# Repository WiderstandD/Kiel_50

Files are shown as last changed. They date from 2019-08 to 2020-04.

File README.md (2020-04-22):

# Kiel_50 - Programmable ESC for the BLDC and PMSM Motors
Kiel 50 is an Arduino UNO shield for driving sensor-less three-phase BLDC motor. The main advantage is the sinusoidal current drive. By monitoring the back-EMF (BEMF) the motor can run without the independent rotor position sensor aka hall sensor or encoder. The chip is able to sense the BEMF from very low rpm up to high rpm. The speed can be set and adjusted using PWM or SPI. The Kiel 50 shield comes with the main chip [A4964](https://www.allegromicro.com/en/Products/Motor-Drivers/BLDC-Drivers/A4964) from "Allegro MicroSystems". This chip is All-in-one: the motor controller, N-Channel MOSFET driver, voltage regulator, MCU watchdog. The ability to program this chip via SPI using Arduino makes it easy to use for many projects. After the configurations were uploaded to the controller and saved to the NVM it can run without Arduino as well.

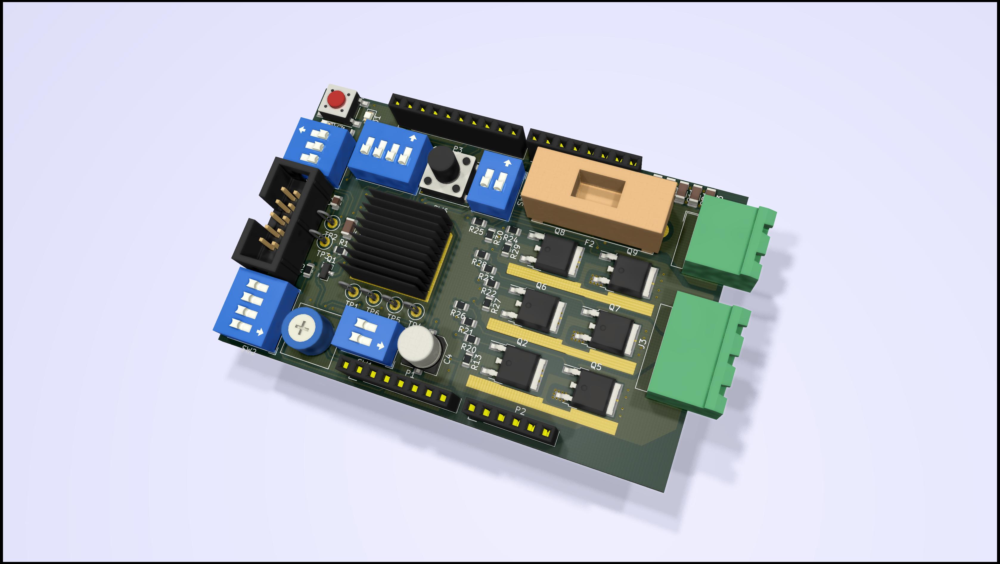
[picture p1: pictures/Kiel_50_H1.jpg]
Board_1

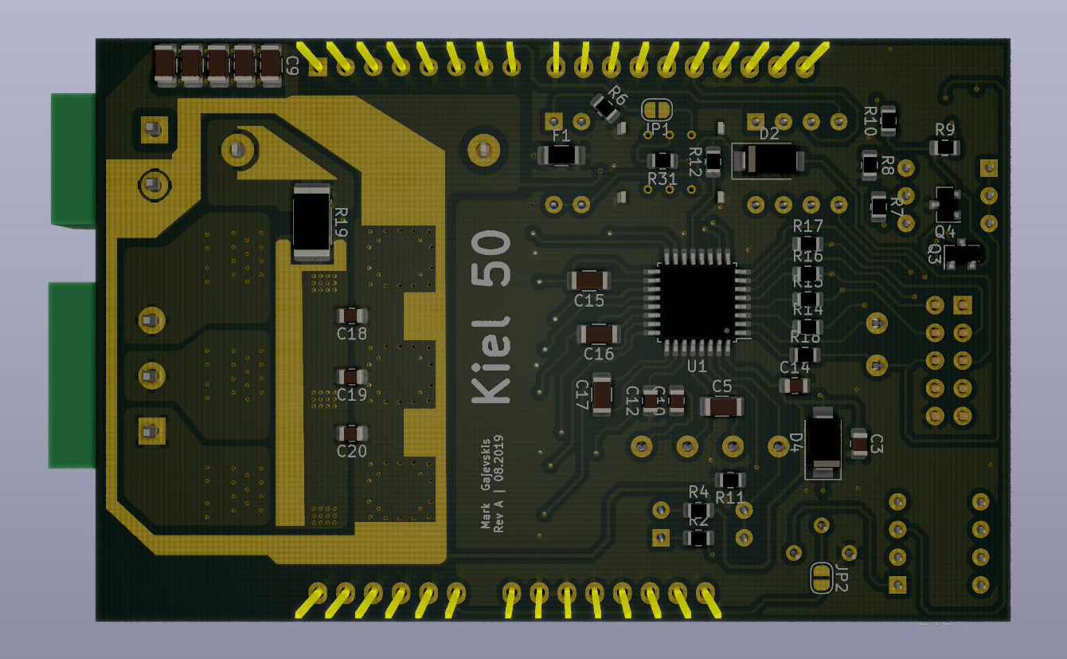
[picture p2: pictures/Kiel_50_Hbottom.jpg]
Board_2

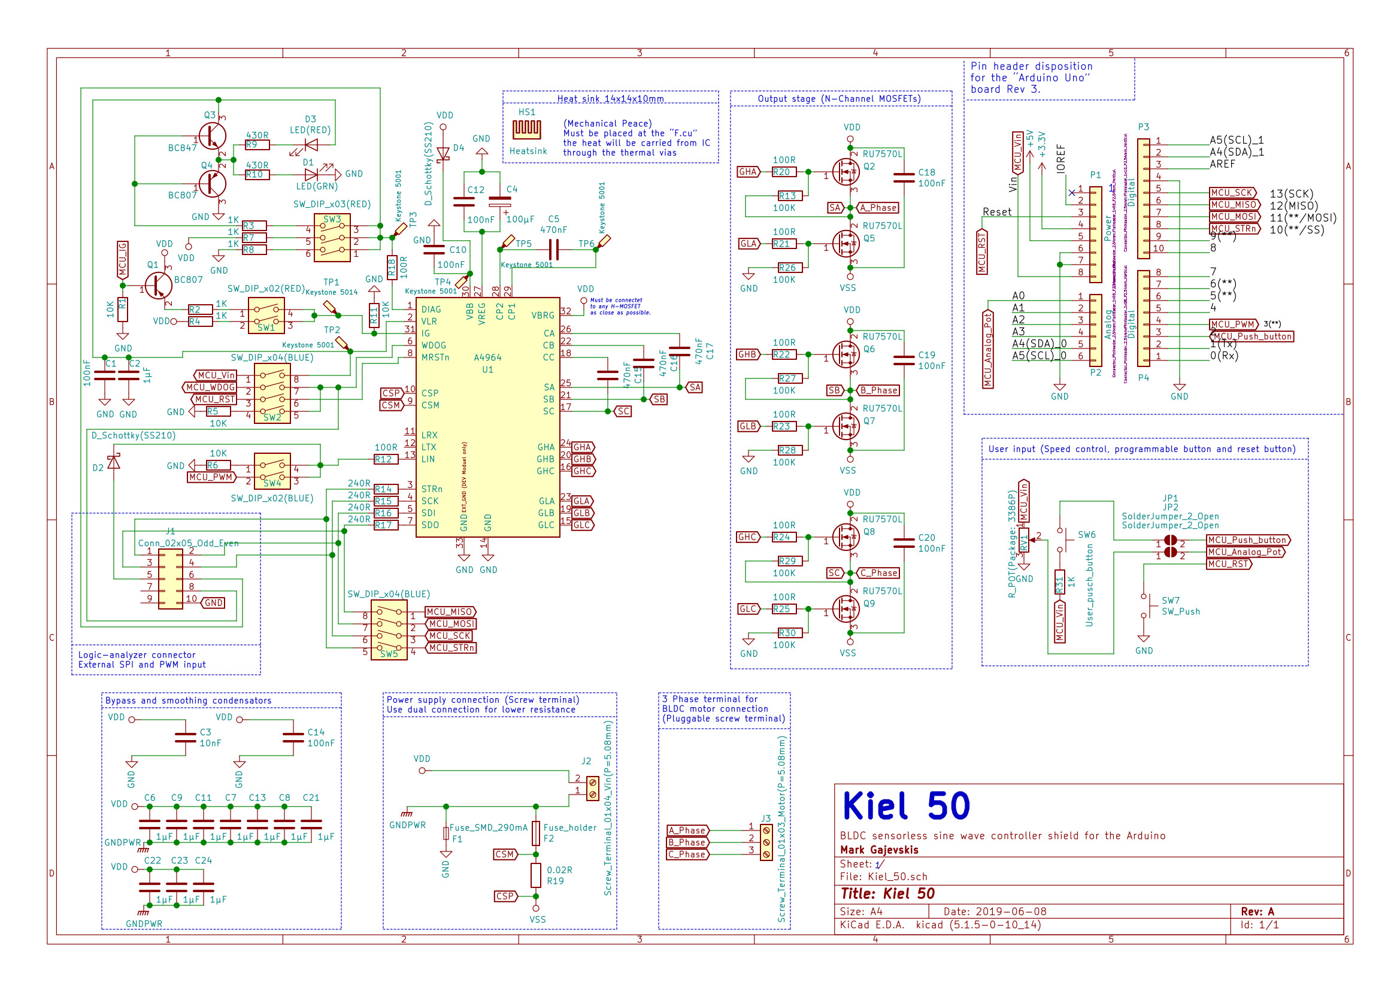
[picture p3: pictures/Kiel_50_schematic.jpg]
Board_3


Measurement of the three-phase (Voltage Ch.1,2,3)

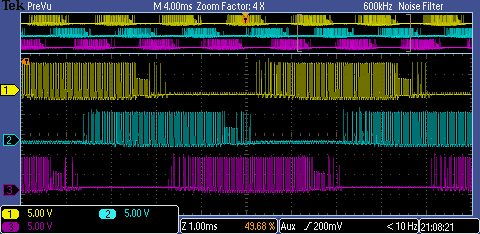
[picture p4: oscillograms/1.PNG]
Measurement1


Measurment of the three-phase (Voltage Ch.1,2,3 + Current Ch.4 (GN))
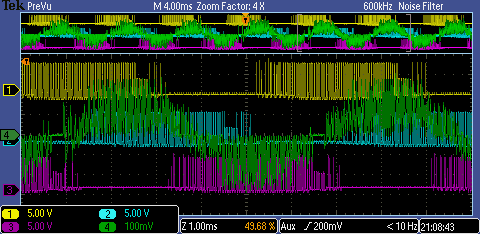
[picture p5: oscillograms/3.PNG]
Measurement2


---

# Technical specification
|Characteristic|Symbol|Note|Raiting|Unit|
| --- | --- | --- | --- | --- |
|Supply voltage|Vsup| |5.5 - 50|V|
|Logic voltage|VLR|REG 25 - VLR|3.3 - 5|V|
|Maximal current|Imax|Fused: F2|10|A|
|Maximal logic current|Ilog|Fused: F1|290|mA|
|Gate drive regulator voltage|Vrg|REG 25 - VRG|8 or 11|V|
|Bridge PWM frequency|ƒpw|REG 0 - PW|14.2 - 50|Khz|
|PWM frequency (logic)|ƒpwm||500 - 1000|Hz|
|SPI frequency|ƒspi||2|Mhz|

# Safety features
|Feature|Description|
| --- | --- |
|Undervoltage lockout|Controller can detect the voltgae drop and switsch the motor off. Thus avoiding the risk of unpredictible behavior.|
|Peak current limit|Can be programmed using the MCU. Uses shunt for monitoring the current.|
|Ignition switch|The high-active input permitt the system start|
|Bridge MOSFET test|The controller can detect if the driving MOSFETs are broken or have any issues.|
|Windmill detection|If the motor rotetes, the controller can detect its speed and syncronise with it. Thus allowing further rotation without the braiking.|  
|MCU watchdog and reset||

# Driving modes
| Mode | Description |
| --- | --- |
| Closed-loop speed | Is used in many e-bike controllers. Acceleration, braking, reaction speed and others settings can be configured via SPI only. After the configuration was set, the speed input via SPI or PWM is acceptable. |
| Closed-loop current | The configuration is done via SPI only. The speed can be adjusted using SPI or PWM. | 
| Open-loop speed | The controller ignores the BEMF and keeps switchting the phases based ont the values of the ramp table. |

#### Hardware design features: 
1. Min component size 0802 SMD for easy hand soldering.
2. Radiator for the heat dissipation from the IC.
---

# How to start

### Hardware for the first start
- Kiel_50 board
- Three phase BLDC motor
- Arduino UNO
- Power supply 5.5V - 50V with at least 1A (for small motors)
- Main PC for programming

### Software for the first start
- Arduino IDE
- The Software for the Arduino UNO 

### Before start, test the board
1. First git clone the repository or download it to the main PC.
2. Navigate to the Kiel_50 folder.
3. Open /Kiel_50/Software/chip_test/chip_test_programm.ino file in Arduino IDE.
4. Select Arduoino UNO in the Borard manger and compile the chip_test_programm.ino.
5. By setting all switches on SW_DIP_x04(BLUE) to ON you enable the SPI communication with Arduino UNO.
6. Plug the Kiel 50 shield to Arduino UNO.
7. Flash Arduino UNO.
8. Connect the power supply to the board, avoid connectong the motor to the board.
9. Open the serial monitor, now you can monitor the supply voltage, chip temperatur, etc.
10. You can try to change the supply voltage (if it's possible). You have to see the voltage change in serial. 

### Frirst start
//ToDo 

---
# Keywords:
- ESC - electric speed controller
- BLDC - Brushless DC electric motor
- PMSM - Permanent magnet synchronous motor
- DC - Direct current
- IDE - Integrated Development Environment
---

# Notes:
#### Aplication example: 
1. Free rotating motors
2. Pump 
3. Fans and blowers

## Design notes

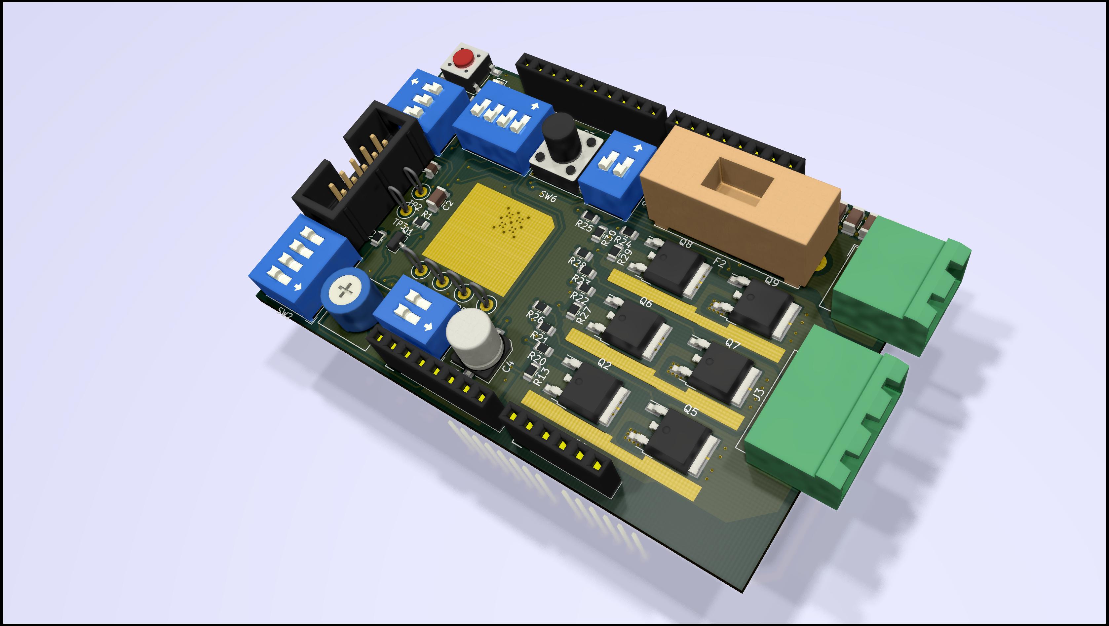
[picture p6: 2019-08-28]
pictures/Kiel_50_3(without_heatsink).jpg

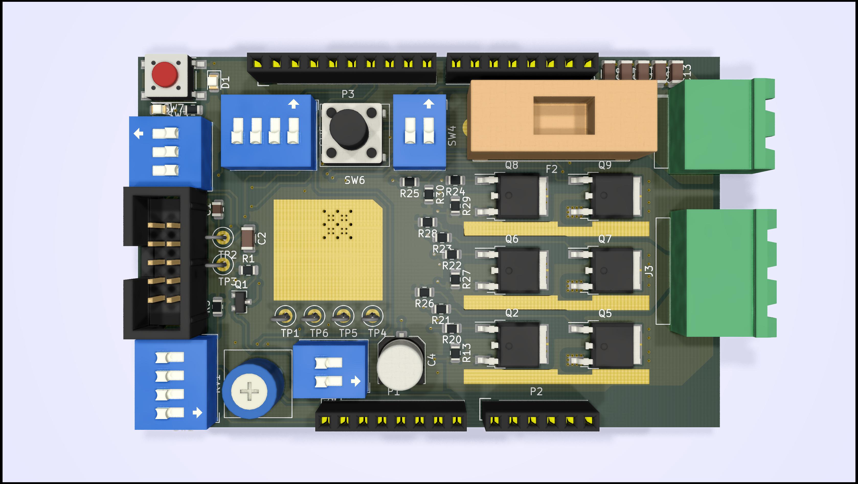
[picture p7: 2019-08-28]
pictures/Kiel_50(without_heatsink).jpg

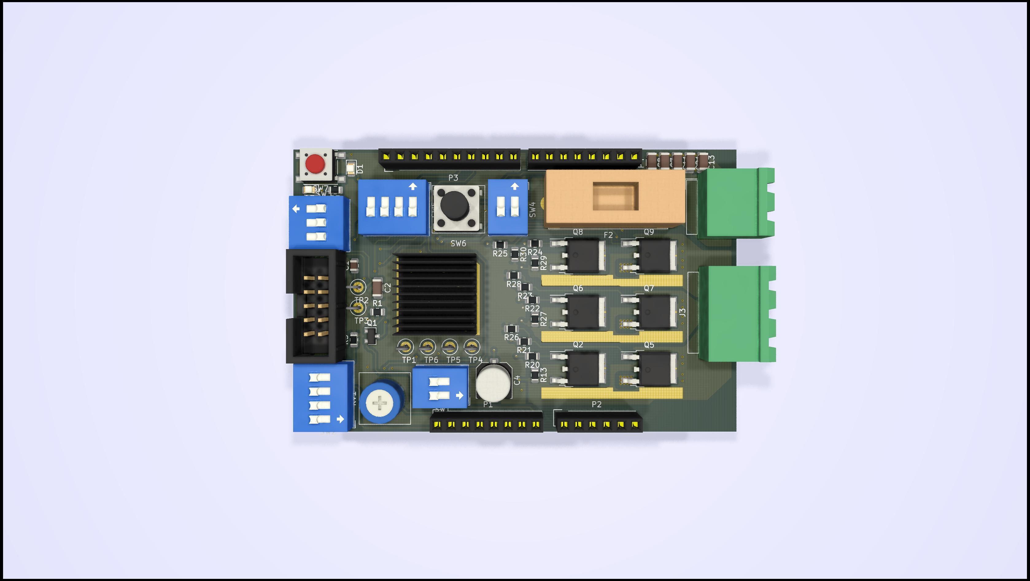
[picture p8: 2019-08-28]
pictures/Kiel_50_H2.jpg

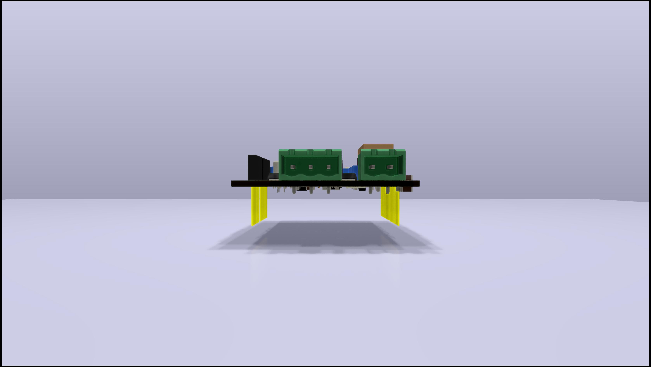
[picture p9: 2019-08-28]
pictures/Kiel_50_Hright.jpg

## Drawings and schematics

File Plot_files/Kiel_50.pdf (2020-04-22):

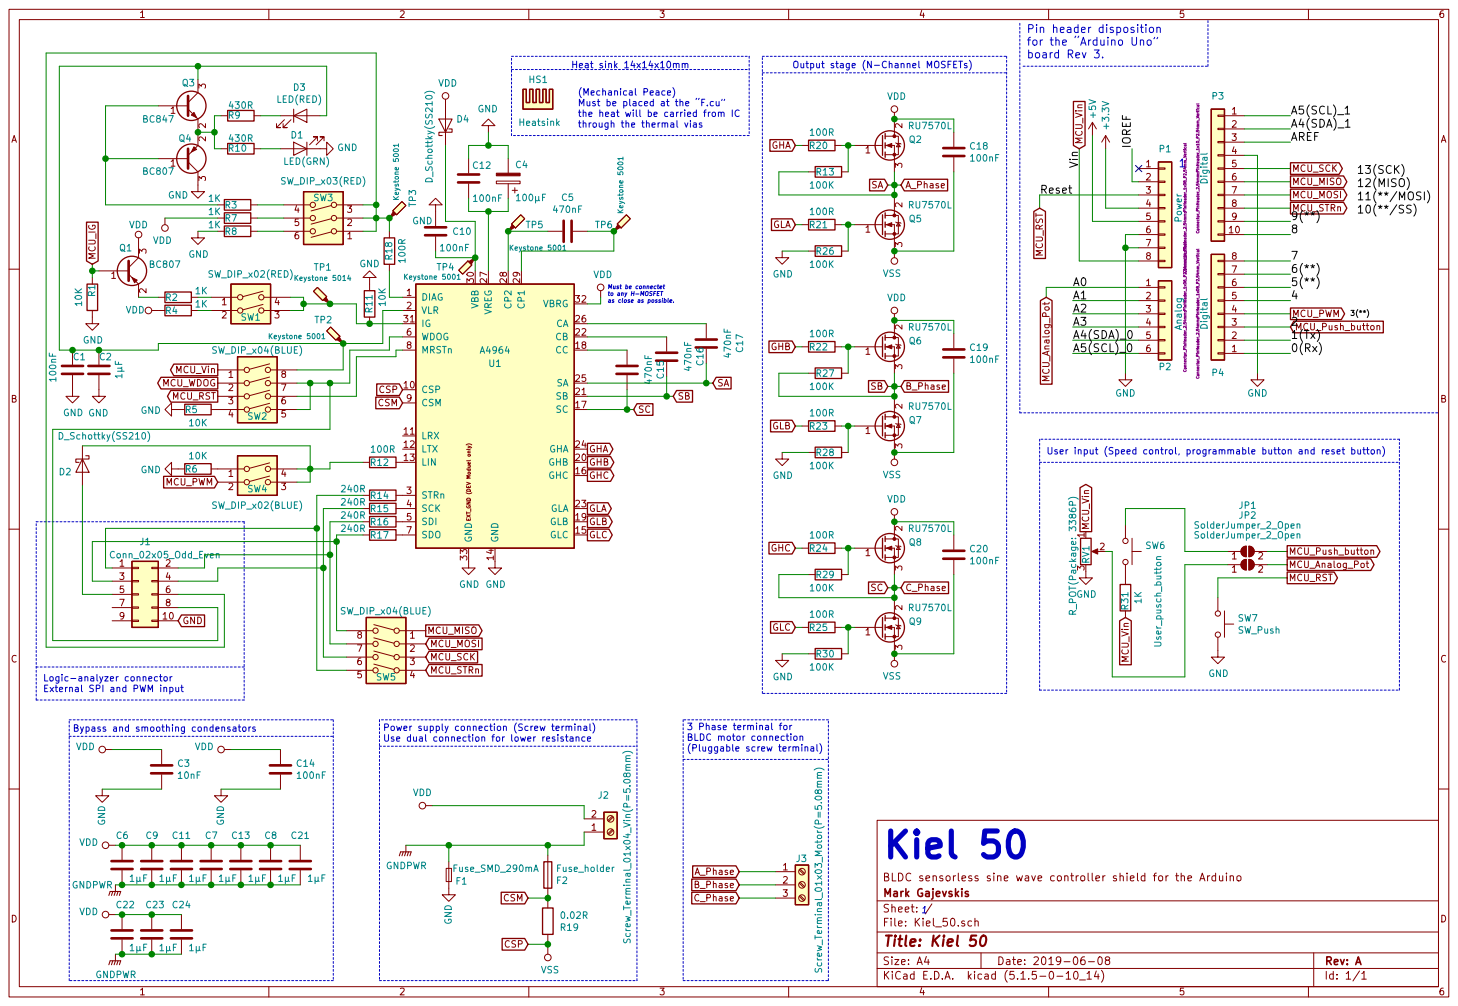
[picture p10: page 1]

Pin header disposition
for the Arduino Uno
9 P3 Digital Connector_PinHeader_2.54mm:PinHeader_1x10_P2.54mm_Vertical 1
SB GHB GHA

board Rev 3. Must be connectet

User input (Speed control, programmable button and reset button) Heat sink 14x14x10mm

Output stage (N-Channel MOSFETs)

(Mechanical Peace)
Must be placed at the F.cu
the heat will be carried from IC
through the thermal vias

Logic-analyzer connector
External SPI and PWM input

Bypass and smoothing condensators

Power supply connection (Screw terminal) Use dual connection for lower resistance

3 Phase terminal for BLDC motor connection

File: Kiel_50.sch Sheet: / Mark Gajevskis BLDC sensorless sine wave controller shield for the Arduino C24

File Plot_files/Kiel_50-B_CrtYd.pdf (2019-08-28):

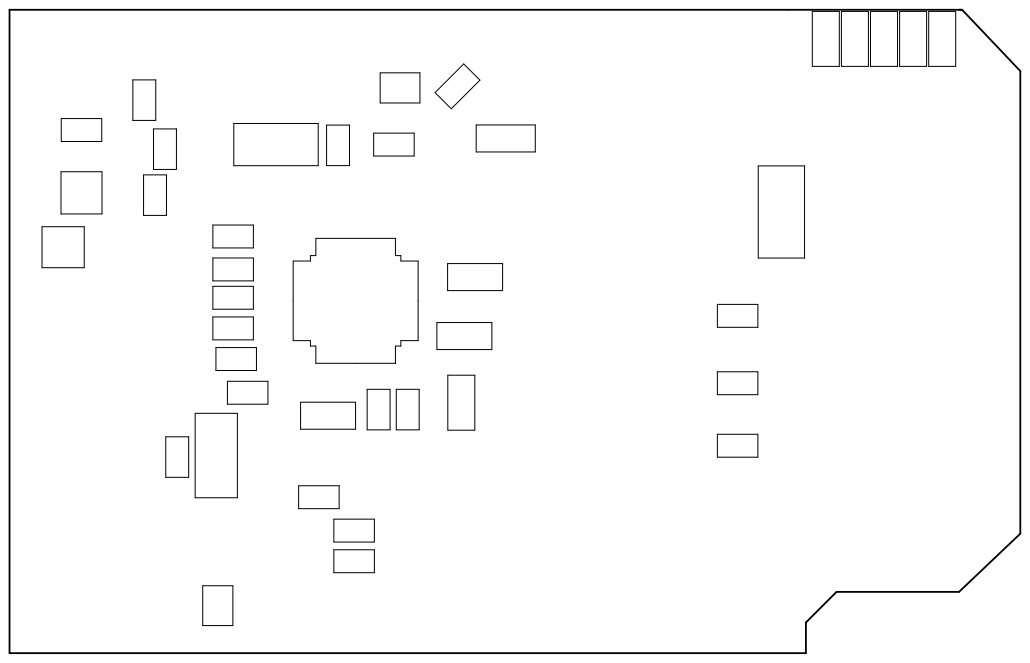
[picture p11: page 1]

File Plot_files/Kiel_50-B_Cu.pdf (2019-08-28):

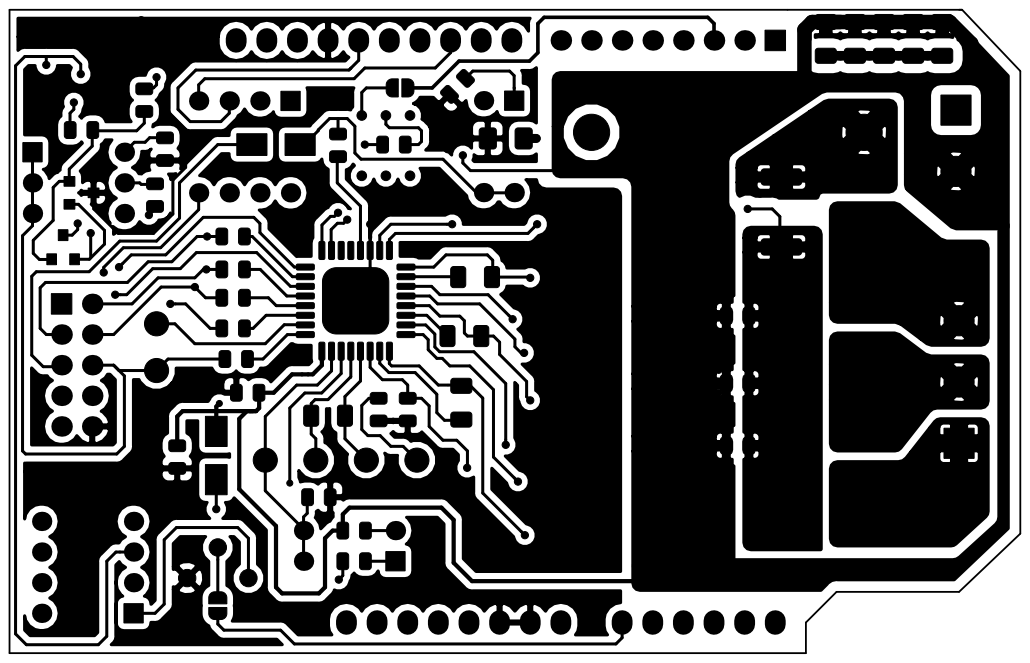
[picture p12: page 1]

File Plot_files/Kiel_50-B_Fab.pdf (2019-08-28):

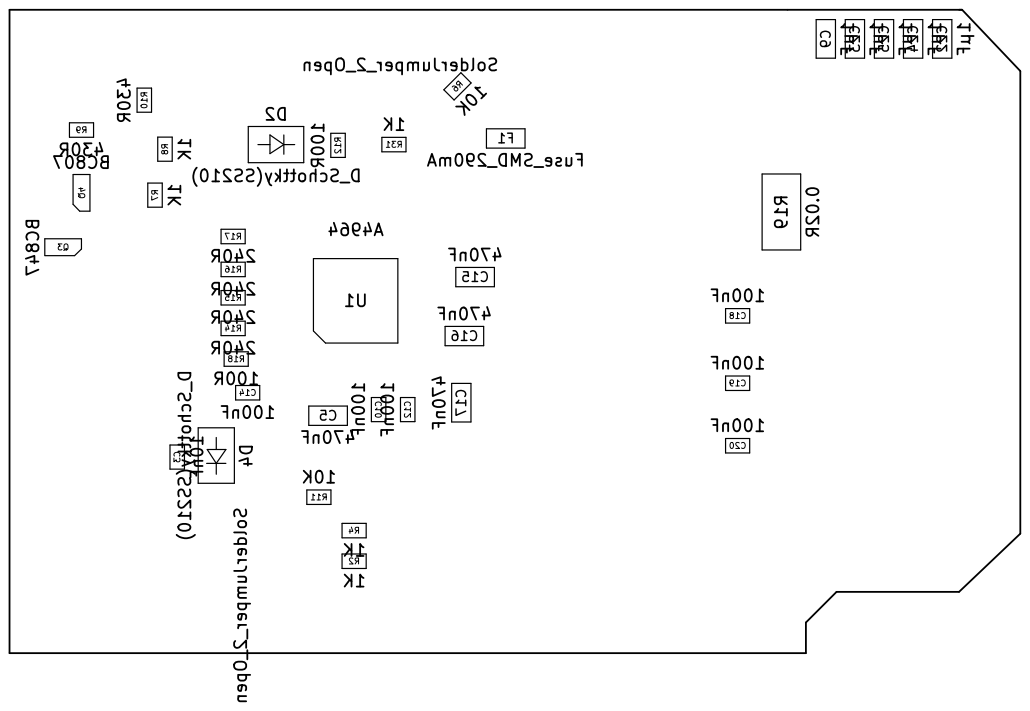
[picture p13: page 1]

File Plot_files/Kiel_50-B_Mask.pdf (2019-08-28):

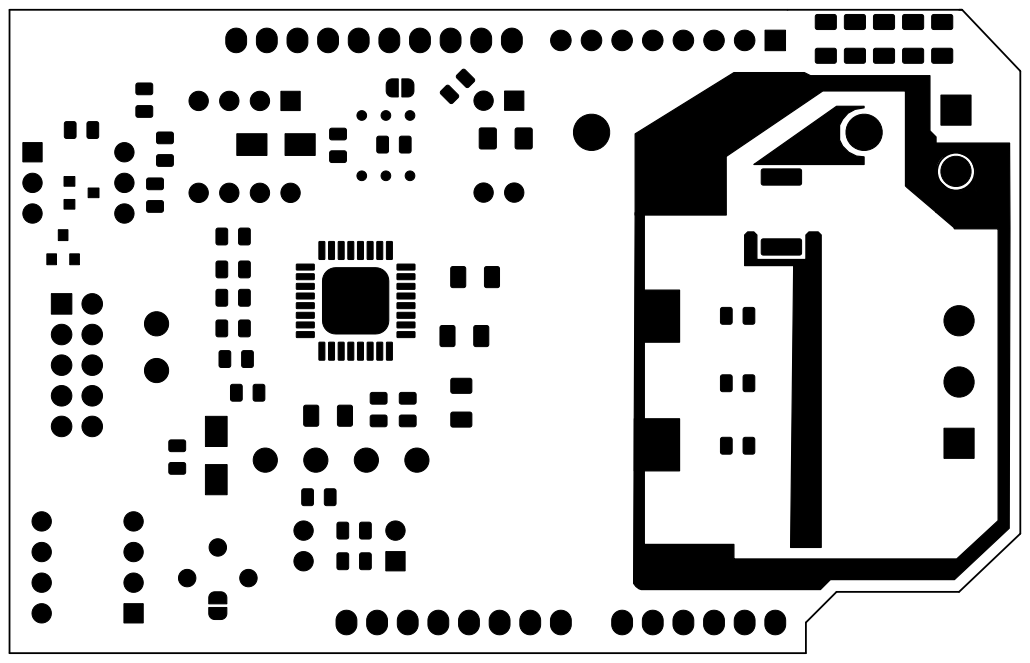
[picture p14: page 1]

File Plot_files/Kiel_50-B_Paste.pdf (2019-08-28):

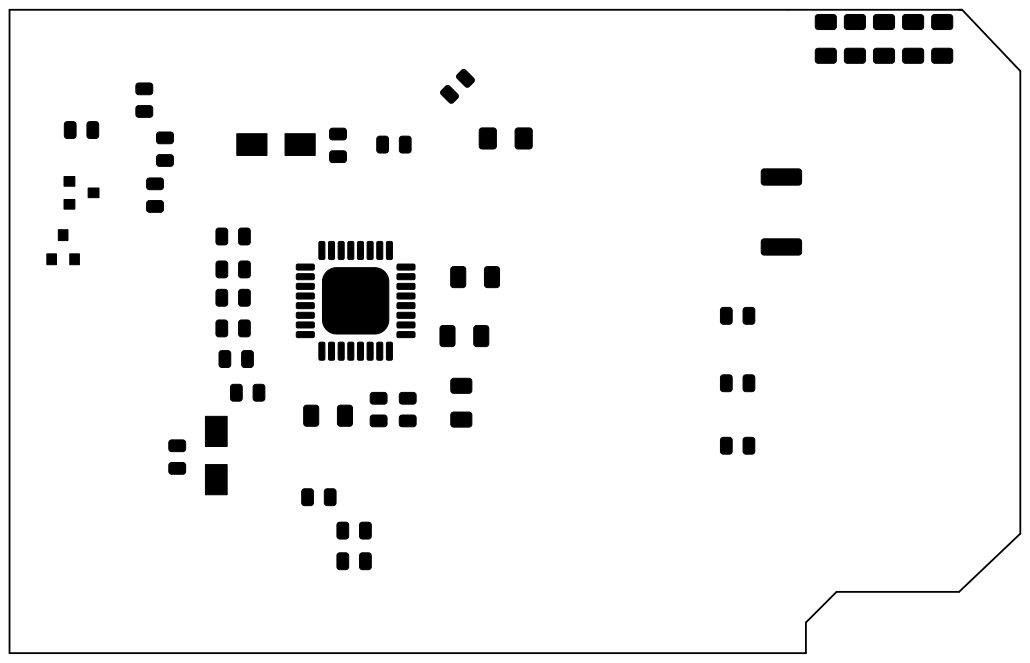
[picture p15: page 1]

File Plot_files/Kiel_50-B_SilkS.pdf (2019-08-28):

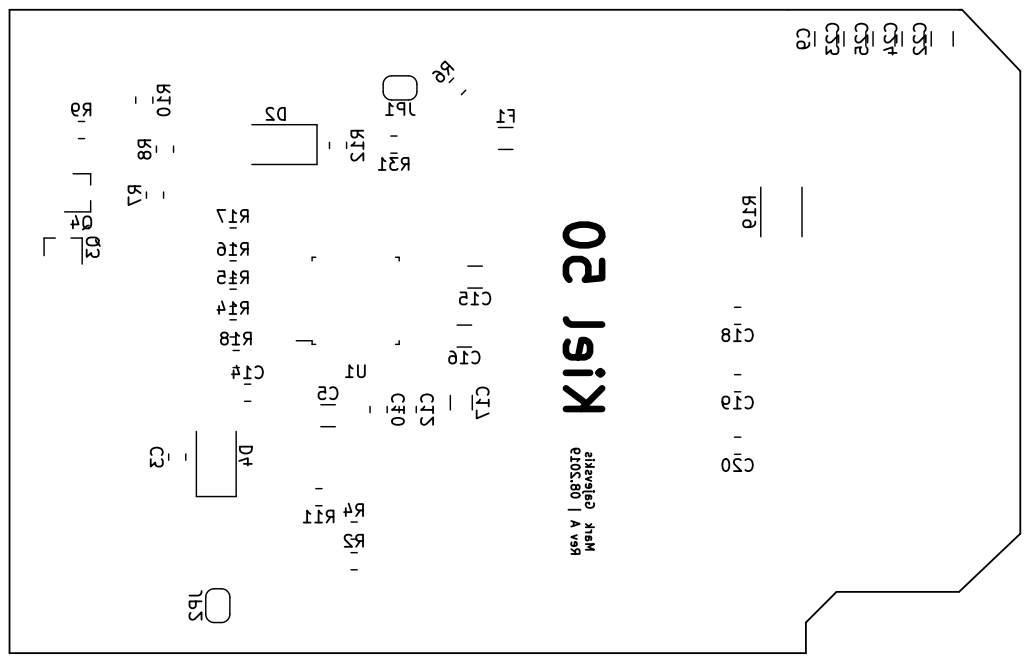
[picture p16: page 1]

Rev A | 08.2019 Mark Gajevskis Kiel 50 U1 C23 C25 C24 C22 C14 C9 C3 R19 JP2

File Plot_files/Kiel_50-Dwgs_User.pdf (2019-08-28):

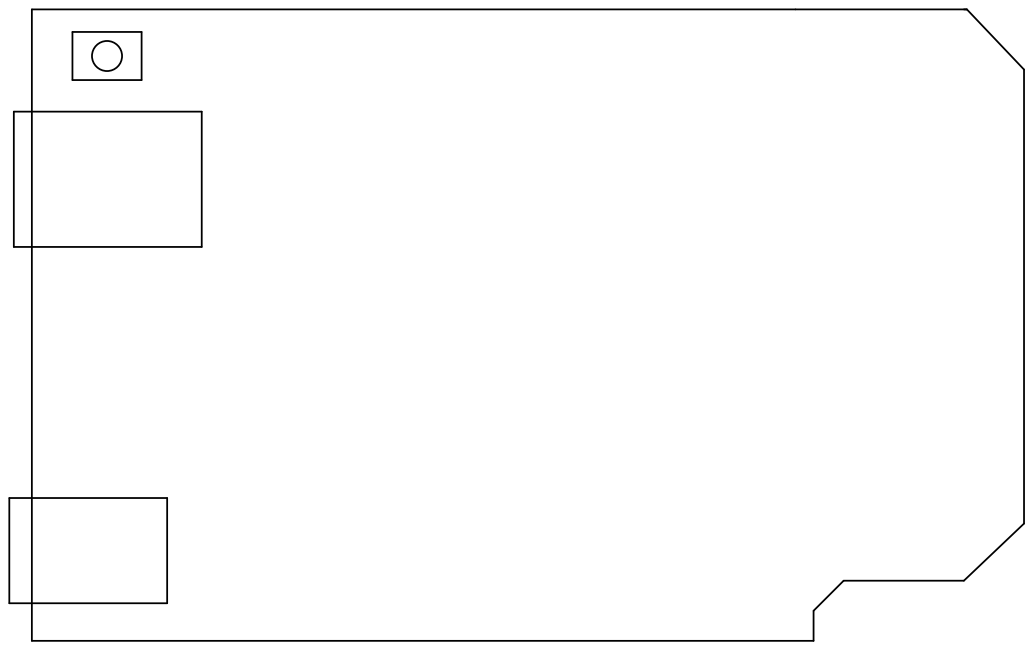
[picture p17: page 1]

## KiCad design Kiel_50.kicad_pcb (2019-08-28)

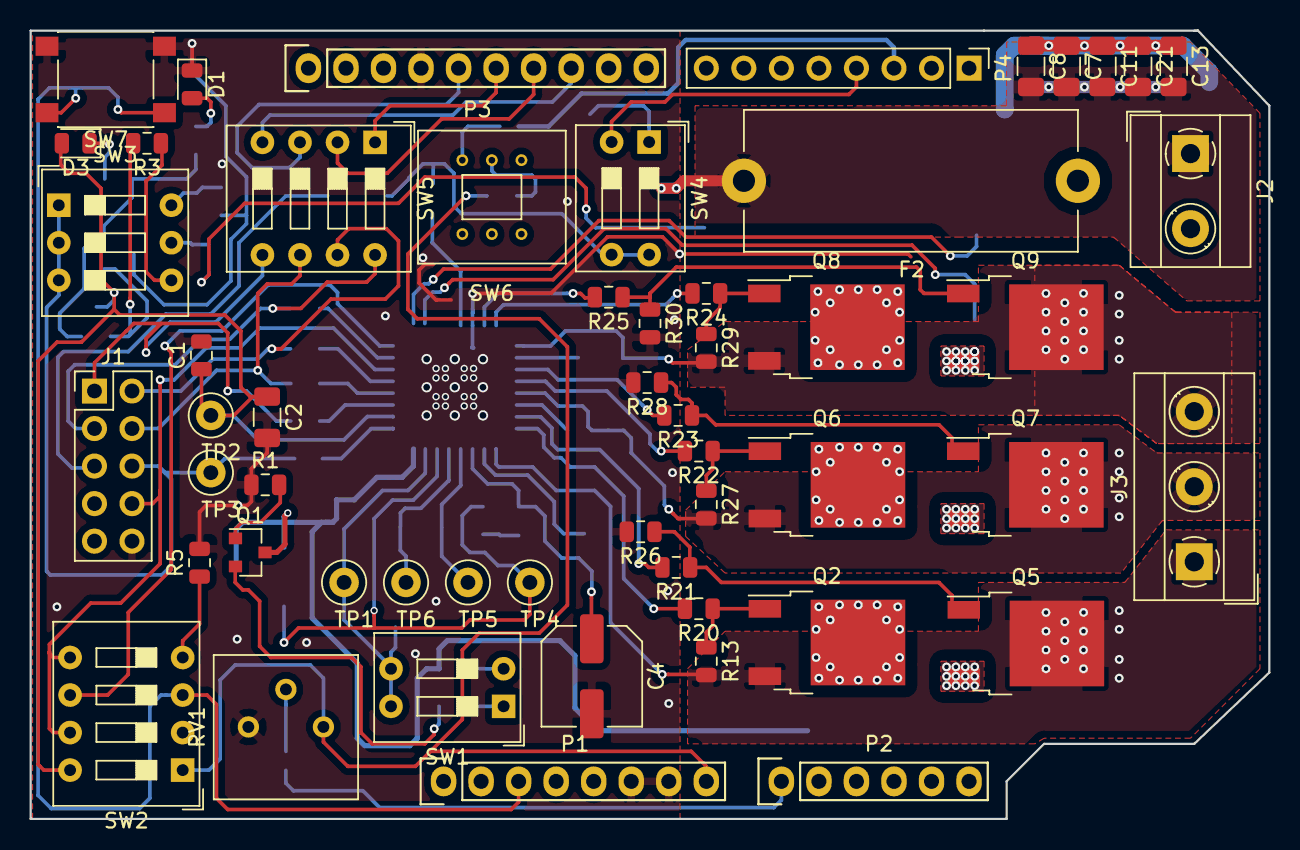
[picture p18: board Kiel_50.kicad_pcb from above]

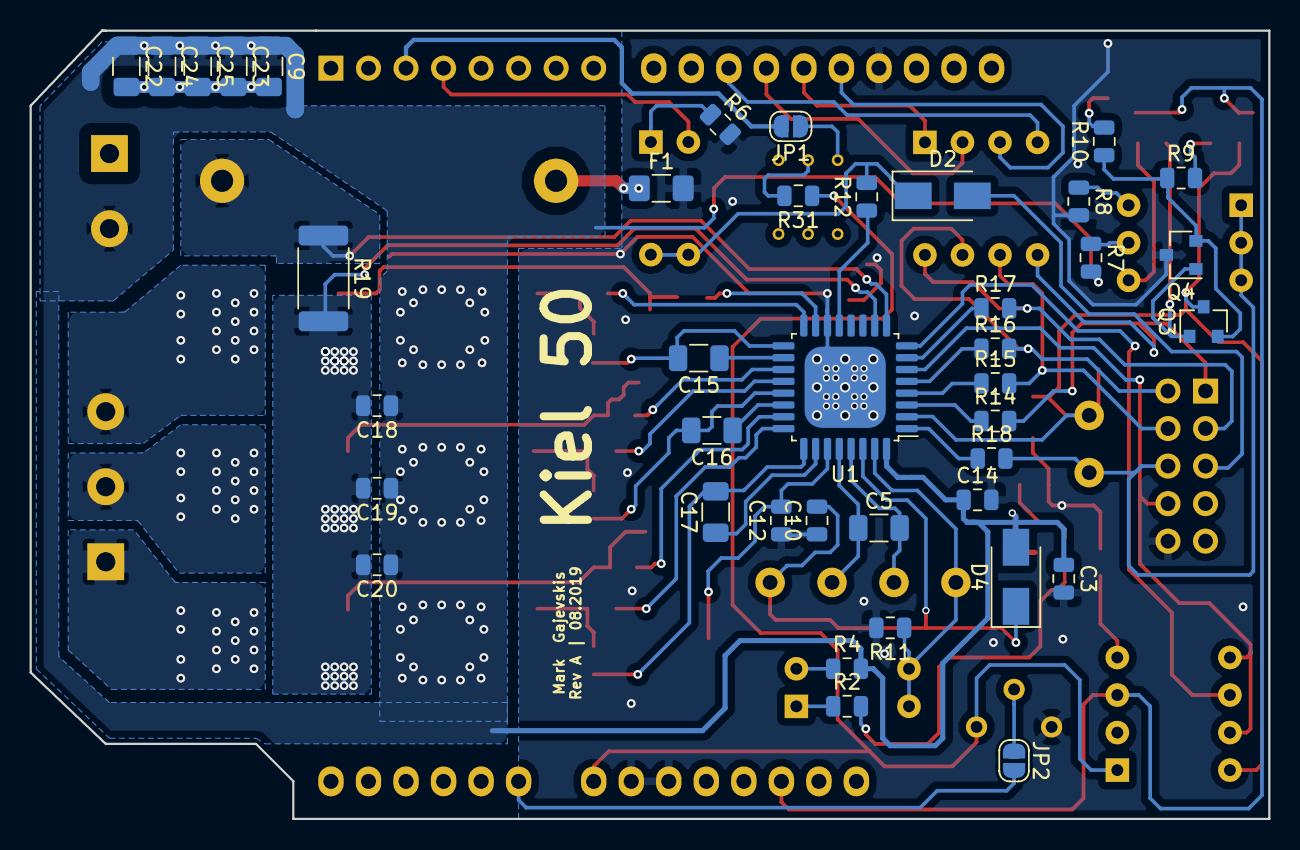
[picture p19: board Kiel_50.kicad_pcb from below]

Board: 2 copper layers, 83.8 x 53.3 mm, 94 parts (40 on the bottom side), 69 nets.

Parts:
C1, C10, C12, C14, C18, C19, C20: 100nF; C_0805_2012Metric
C2, C7, C8, C9, C11, C13, C21, C22, C23, C24, C25: 1µF; C_1206_3216Metric
C3: 10nF; C_0805_2012Metric
C4: 100µF; C_Elec_6.3x7.7
C5, C15, C16, C17: 470nF; C_1206_3216Metric
D1: LED(GRN); LED_0805_2012Metric
D2, D4: D_Schottky(SS210); D_SMA
D3: LED(RED); LED_0805_2012Metric
F1: Fuse_SMD_290mA; Fuse_1206_3216Metric_Pad1.42x1.75mm_HandSolder
F2: Fuse_10A; Fuseholder_Cylinder-5x20mm_Stelvio-Kontek_PTF78_Horizontal_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
J1: Conn_02x05_Odd_Even; PinHeader_2x05_P2.54mm_Vertical
J2: Screw_Terminal_01x04_Vin(P=5.08mm); TerminalBlock_MetzConnect_Type101_RT01602HBWC_1x02_P5.08mm_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
J3: Screw_Terminal_01x03_Motor(P=5.08mm); TerminalBlock_MetzConnect_Type101_RT01603HBWC_1x03_P5.08mm_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
JP1, JP2: SolderJumper_2_Open; SolderJumper-2_P1.3mm_Open_RoundedPad1.0x1.5mm
P1: Power; Socket_Strip_Arduino_1x08
P2: Analog; Socket_Strip_Arduino_1x06
P3: Digital; Socket_Strip_Arduino_1x10
P4: Digital; PinHeader_1x08_P2.54mm_Vertical
Q1, Q4: BC807; SOT-23
Q2, Q5, Q6, Q7, Q8, Q9: RU7570L; TO-252-2
Q3: BC847; SOT-23
R1, R5, R6, R11: 10K; R_0805_2012Metric
R2, R3, R4, R7, R8, R31: 1K; R_0805_2012Metric
R9, R10: 430R; R_0805_2012Metric
R12, R18, R20, R21, R22, R23, R24, R25: 100R; R_0805_2012Metric
R13, R26, R27, R28, R29, R30: 100K; R_0805_2012Metric
R14, R15, R16, R17: 240R; R_0805_2012Metric
R19: 0.02R; R_2512_6332Metric
RV1: R_POT(Package: 3386P); Potentiometer_Bourns_3386P_Vertical
SW1: SW_DIP_x02(RED); SW_DIP_SPSTx02_Slide_9.78x7.26mm_W7.62mm_P2.54mm
SW2, SW5: SW_DIP_x04(BLUE); SW_DIP_SPSTx04_Slide_9.78x12.34mm_W7.62mm_P2.54mm
SW3: SW_DIP_x03(RED); SW_DIP_SPSTx03_Slide_9.78x9.8mm_W7.62mm_P2.54mm
SW4: SW_DIP_x02(BLUE); SW_DIP_SPSTx02_Slide_9.78x7.26mm_W7.62mm_P2.54mm
SW6: User_pusch_button; XKB7070-Z-92
SW7: SW_Push; SW_Push_1P1T_NO_6x6mm_H9.5mm
TP1: Keystone 5014; TestPoint_Loop_D2.50mm_Drill1.0mm
TP2, TP3, TP4, TP5, TP6: Keystone 5001; TestPoint_Loop_D2.50mm_Drill1.0mm
U1: A4964; LQFP-32_7x7mm_P0.8mm_with_heat_pad

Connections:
A_Phase: C17.2, J3.1, Q2.3, Q5.2, R13.2, U1.25
B_Phase: C16.2, J3.2, Q6.3, Q7.2, R27.2, U1.21
CSM: F2.1, R19.1, U1.9
CSP: C18.2, C19.2, C20.2, Q5.3, Q7.3, Q9.3, R19.2, U1.10
C_Phase: C15.2, J3.3, Q8.3, Q9.2, R29.2, U1.17
GHA: R20.2, U1.24
GHB: R22.2, U1.20
GHC: R24.2, U1.16
GLA: R21.2, U1.23
GLB: R23.2, U1.19
GLC: R25.2, U1.15
GND: C1.2, C2.2, C3.2, C4.2, C10.1, C12.1, C14.2, D1.1, F1.2, J1.10, P1.6, P1.7, P3.4, Q4.3, R1.1, R5.2, R6.2, R8.2, R11.2, R26.2, R28.2, R30.2, RV1.3, SW7.2, U1.14, U1.33
GNDPWR: C7.2, C8.2, C9.2, C11.2, C13.2, C21.2, C22.2, C23.2, C24.2, C25.2, F1.1, F2.2, J2.1
MCU_Analog_Pot: JP2.2, P2.1
MCU_IG: Q1.1, R1.2
MCU_MISO: P3.6, SW5.1
MCU_MOSI: P3.7, SW5.2
MCU_PWM: P4.4, SW4.2
MCU_Push_button: JP1.2, P4.3
MCU_RST: P1.3, SW2.3, SW7.1
MCU_SCK: P3.5, SW5.3
MCU_STRn: P3.8, SW5.4
MCU_Vin: P1.8, R31.1, RV1.1, SW2.1
unnamed: C1.1, C2.1, D3.2, Q3.3, SW2.8, TP2.1, U1.2
unnamed: C5.1, TP5.1, U1.28
unnamed: C5.2, TP6.1, U1.29
unnamed: C10.2, D4.1, TP4.1, U1.30
unnamed: C4.1, C12.2, U1.27
unnamed: C15.1, U1.18
unnamed: C16.1, U1.22
unnamed: C17.1, U1.26
unnamed: D1.2, R10.2
unnamed: D2.1, R12.2, SW4.3, SW4.4
unnamed: D2.2, J1.5
unnamed: D3.1, R9.2
unnamed: J1.1, R14.2, SW5.5
unnamed: J1.2, R16.2, SW5.7
unnamed: J1.3, R17.2, SW5.8
unnamed: J1.4, R15.2, SW5.6
unnamed: J1.6, R18.2, SW3.1, SW3.2, SW3.3, TP3.1
unnamed: J1.8, SW2.5, SW2.7, U1.6
unnamed: JP1.1, SW6.1
unnamed: JP2.1, RV1.2
unnamed: Q1.2, R2.2
unnamed: Q2.1, R13.1, R20.1
unnamed: Q3.1, Q4.1, R3.2
unnamed: Q3.2, Q4.2, R9.1, R10.1
unnamed: Q5.1, R21.1, R26.1
unnamed: Q6.1, R22.1, R27.1
unnamed: Q7.1, R23.1, R28.1
unnamed: Q8.1, R24.1, R29.1
unnamed: Q9.1, R25.1, R30.1
unnamed: R2.1, SW1.1
unnamed: R3.1, SW3.4
unnamed: R4.1, SW1.2
unnamed: R5.1, SW2.4
unnamed: R6.1, SW4.1
unnamed: R7.1, SW3.5
unnamed: R8.1, SW3.6
unnamed: R11.1, SW1.3, SW1.4, TP1.1, U1.31
unnamed: R12.1, U1.13
unnamed: R14.1, U1.3
unnamed: R15.1, U1.4
unnamed: R16.1, U1.5
unnamed: R17.1, U1.7
unnamed: R18.1, U1.1
unnamed: R31.2, SW6.2
unnamed: SW2.6, U1.8
VDD: C3.1, C7.1, C8.1, C9.1, C11.1, C13.1, C14.1, C18.1, C19.1, C20.1, C21.1, C22.1, C23.1, C24.1, C25.1, D4.2, J2.2, Q1.3, Q2.2, Q6.2, Q8.2, R4.2, R7.2, U1.32

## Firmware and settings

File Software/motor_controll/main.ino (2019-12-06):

/*
 * Author: Mark Gajevskis
 * Date: 9 March 2019
 * Board: Arduino UNO
 * Chip: A4964
 * Communication protocol: 4-wire HW SPI
 * Logic voltage: 5V
 * Logic voltage shiftig: NO
 * USART baudrate: 115200
 * 
 * 
 * 
 * This code write the "Register Select" in 
 * order to set the register 31 in Read Only 
 * mode. The data is send to the host pc via UART.
 * 
 * 
 */

#include "Arduino.h"
#include "main.h"
#include "SPI.h"
#include "motor_settings.h"


uint16_t countSetBits(unsigned int n)
{
  unsigned int count = 0;
  while (n)
  {
    count += n & 1;
    n >>= 1;
  }
  return count;
}

void dialup(uint16_t addr, uint16_t val) {

  foo = (addr | SPI_WRITE | val);
  count = countSetBits(foo);

  if ((count % 2) == 0) {
    foo2 = (foo | PARITY);
    Serial.print("if passed, counter: ");
    Serial.println(count);
    Serial.print("parity result: ");
    Serial.println(foo2, BIN);

    SPI.beginTransaction(SPISettings(SPI_SPEED, MSBFIRST, SPI_MODE3));
    digitalWrite(PIN_CS, LOW);
    SPI.transfer16(foo2);
    digitalWrite(PIN_CS, HIGH);
  }
  else {
    Serial.print("else...no parity: ");
    Serial.println(foo, BIN);

    SPI.beginTransaction(SPISettings(SPI_SPEED, MSBFIRST, SPI_MODE3));
    digitalWrite(PIN_CS, LOW);
    SPI.transfer16(foo);
    digitalWrite(PIN_CS, HIGH);
  }
  Serial.println("dialup_end");
}

void temperature() {

  SPI.beginTransaction(SPISettings(SPI_SPEED, MSBFIRST, SPI_MODE3)); // Start SPI dialog with settings for A4964
  digitalWrite(PIN_CS, LOW);
  SPI.transfer16(REG_BRS_TEMP);  // Write the RBS in temperature rading mode
  digitalWrite(PIN_CS, HIGH);

  SPI.beginTransaction(SPISettings(SPI_SPEED, MSBFIRST, SPI_MODE3)); // Start SPI dialog with settings for A4964
  digitalWrite(PIN_CS, LOW);
  rdng_temp = SPI.transfer16(REG_RD_ONLY);  // Read the register 31
  digitalWrite(PIN_CS, HIGH);

  Serial.print("Temperature: ");
  Serial.println((367.7 - ((rdng_temp & 0b11111111110) >> 1) * 0.451), 2); // Refer to A4964 manual page 77
}

void showspeed() {

  SPI.beginTransaction(SPISettings(SPI_SPEED, MSBFIRST, SPI_MODE3)); // Start SPI dialog with settings for A4964
  digitalWrite(PIN_CS, LOW);
  SPI.transfer16(REG_RBS_SPEED);  // Write the RBS in temperature rading mode
  digitalWrite(PIN_CS, HIGH);

  SPI.beginTransaction(SPISettings(SPI_SPEED, MSBFIRST, SPI_MODE3)); // Start SPI dialog with settings for A4964
  digitalWrite(PIN_CS, LOW);
  rdng_speed = SPI.transfer16(REG_RD_ONLY);  // Read the register 31
  digitalWrite(PIN_CS, HIGH);

  Serial.print("Speed (rpm): ");
  Serial.println((((((rdng_speed & 0b11111111110) >> 1) * 1.6) * 60) / 7), 4); // Refer to A4964 manual page 77

  SPI.beginTransaction(SPISettings(SPI_SPEED, MSBFIRST, SPI_MODE3)); // Start SPI dialog with settings for A4964
  digitalWrite(PIN_CS, LOW);
  rdng_speed = SPI.transfer16(REG_RD_ONLY);  // Read the register 31
  digitalWrite(PIN_CS, HIGH);

  Serial.print("Speed (Hz): ");
  Serial.println((((rdng_speed & 0b11111111110) >> 1) * 1.6), 4); // Refer to A4964 manual page 77
}

void duty_cycle() {

  SPI.beginTransaction(SPISettings(SPI_SPEED, MSBFIRST, SPI_MODE3)); // Start SPI dialog with settings for A4964
  digitalWrite(PIN_CS, LOW);
  SPI.transfer16(REG_RBS_DUTY_CYCLE);  // Write the RBS in voltage rading mode
  digitalWrite(PIN_CS, HIGH);

  SPI.beginTransaction(SPISettings(SPI_SPEED, MSBFIRST, SPI_MODE3)); // Start SPI dialog with settings for A4964
  digitalWrite(PIN_CS, LOW);
  rdng_duty_cycle = SPI.transfer16(REG_RD_ONLY);  // Read the register 31
  digitalWrite(PIN_CS, HIGH);
  Serial.print("Peak Duty Cycle: ");
  Serial.println((((rdng_duty_cycle & 0b11111111110) >> 1) / 1023) * 100, 3);
}

void applied_phase_advance() {

  SPI.beginTransaction(SPISettings(SPI_SPEED, MSBFIRST, SPI_MODE3)); // Start SPI dialog with settings for A4964
  digitalWrite(PIN_CS, LOW);
  SPI.transfer16(REG_RBS_PHASE_ADV);  // Write the RBS in voltage rading mode
  digitalWrite(PIN_CS, HIGH);

  SPI.beginTransaction(SPISettings(SPI_SPEED, MSBFIRST, SPI_MODE3)); // Start SPI dialog with settings for A4964
  digitalWrite(PIN_CS, LOW);
  rdng_phase_adv = SPI.transfer16(REG_RD_ONLY);  // Read the register 31
  digitalWrite(PIN_CS, HIGH);
  Serial.print("Applied Phase Advance: ");
  Serial.println(((rdng_phase_adv & 0b11111111110) >> 1) * 0.7, 3);
}

void voltage() {

  SPI.beginTransaction(SPISettings(SPI_SPEED, MSBFIRST, SPI_MODE3)); // Start SPI dialog with settings for A4964
  digitalWrite(PIN_CS, LOW);
  SPI.transfer16(REG_RBS_VOLT);  // Write the RBS in voltage rading mode
  digitalWrite(PIN_CS, HIGH);

  SPI.beginTransaction(SPISettings(SPI_SPEED, MSBFIRST, SPI_MODE3)); // Start SPI dialog with settings for A4964
  digitalWrite(PIN_CS, LOW);
  rdng_volt = SPI.transfer16(REG_RD_ONLY);  // Read the register 31
  digitalWrite(PIN_CS, HIGH);
  Serial.print("Voltage: ");
  Serial.println(((rdng_volt & 0b11111111110) >> 1) * 0.0528, 3);
}

void current() {

  SPI.beginTransaction(SPISettings(SPI_SPEED, MSBFIRST, SPI_MODE3)); // Start SPI dialog with settings for A4964
  digitalWrite(PIN_CS, LOW);
  SPI.transfer16(REG_RBS_CURRENT);  // Write the RBS in current rading mode
  digitalWrite(PIN_CS, HIGH);

  SPI.beginTransaction(SPISettings(SPI_SPEED, MSBFIRST, SPI_MODE3)); // Start SPI dialog with settings for A4964
  digitalWrite(PIN_CS, LOW);
  rdng_current = SPI.transfer16(REG_RD_ONLY);  // Read the register 31
  digitalWrite(PIN_CS, HIGH);
  Serial.print("Current: ");
  Serial.println(((((rdng_current & 0b11111111110) >> 1) / 50) * 1.76), 3);
}

void writeregisters() {

  dialup(ADDR_PWM_CONF_0, MOD_3 | PMD_CENTER | PW_PWM_FREQ(0b100110));
  //dialup(ADDR_PWM_CONF_1, DS_DITHER_DISABLE),
  dialup(ADDR_PWM_CONF_1, DP_PERIOD_1_2 | DD_TIME_2 | DS_STEP_COUNT_15);
  dialup(ADDR_BRGE_CONF, SA_AMP_GAIN_2_5 | DT_MOSFET_500);
  dialup(ADDR_GATE_DRV_CONF_0, IR1_ON_40 | IR2_ON_10);
  dialup(ADDR_GATE_DRV_CONF_1, IF1_OFF_60 | IF2_OFF_15);
  dialup(ADDR_GATE_DRV_CONF_2, TRS_ON_TIME_300 | TFS_OFF_TIME_600);
  dialup(ADDR_I_LIM_CONF, OBT_BLANK_TIME_3_6 | VIL_SCALE_16_16);
  dialup(ADDR_VDS_0, MIT_TRESHOLD_200 | VT_V_TRESHOLD_1_2);
  dialup(ADDR_VDS_1, VDQ_DEBOUNCE | VQT_QUAL_TIME_1_2);
  dialup(ADDR_WATCH_DOG_0, WM_MIN_TIME_21);
  dialup(ADDR_WATCH_DOG_1, WC_DISABLE);     // Register Nr. 10
  dialup(ADDR_COMMT_0, CP_SS_PROP_GAIN_2 | CP_SS_INTEG_GAIN_2);
  dialup(ADDR_COMMT_1, CPT_TC_PROP_GAIN_2 | CIT_TC_INTEG_GAIN_2);
  dialup(ADDR_BEMF_CONF_0, BW_DETECT_WINDOW(0b11111));
  dialup(ADDR_BEMF_CONF_1, BS_SMPL_CYCLE_6 | BF_WM_FILTER_TIME_200);
  dialup(ADDR_STR_CONF_0, HT_ALIGMENT_400 | HD_PWM_ALIG_3_125);   // Register Nr. 15
  dialup(ADDR_STR_CONF_1, STM_COASM_OFF | RSC_OFF | KM_RATIO_0_30 | HR_DUTY_CYCLE_0);
  dialup(ADDR_STR_CONF_2, WIN_MODE_OFF);
  dialup(ADDR_STR_CONF_3, SF2_FINAL_FREQ_10 | SF1_INITIAL_FREQ_0_5);
  dialup(ADDR_STR_CONF_4, SD2_FINAL_CYC_18_75 | SD1_INITIAL_CYC_6_25);
  dialup(ADDR_STR_CONF_5, STS_STEP_TIME_160 | SFS_FINAL_RAMP_FREQ(0b0011));  // Register Nr. 20
  dialup(ADDR_SPEED_LOOP_0, SGL_ACCELER_LIM(0b00111) | SG_GAIN(0b1000));
  dialup(ADDR_SPEED_LOOP_1, DV_CYCLE_COMP_OFF | DF_DECEL_FACTOR_1 | SR_SPEED_CTRL_RES_0_1);
  dialup(ADDR_SPEED_LOOP_2, SL_LOW_THRESHOLD(0b0001) | SH_HIGH_THRESHOLD(0b1100));
  dialup(ADDR_SYS, ESF_NO_STOP_ON_FAIL | VLR_LOGIC_V_5 | VRG_GATE_V_8 | OPM_STAND_ALONE | LWK_PWM_WAKE_MDOE | IPI_ACT_LOW | DIL_I_LIM_OFF | CM_CLOSED_LOOP_SPEED_2); // REG Nr. 25
  dialup(ADDR_PHA_ADV, PAM_PHASE_ADV_AUTO | KIP_AUTO_PHASE_CTRL_4);
  dialup(ADDR_MOT_FUN, LEN_LIN_STANDBY | GTS_NO_CHANGE_0 | OVM_OVERMOD_OFF | DRM_MODE_SINE | BRK_ON | DIR_REVERSE | RUN_ON);
}

void speedreference(){

  const int analogPin = A0;
  uint16_t A0_val = 0;
  uint16_t A0_conv = 0;
  uint16_t A0_ready = 0;
  // The "A0_val" is 10bit meaning 0 to 1023 dec. long. Need to be converted to 9bit meaning 0 to 511 dec. long.
  A0_val = analogRead(analogPin);
  A0_conv = map(A0_val, 0, 1023, 0, 511);
  // To do: Shift converted value to 1 bit left
  A0_ready = (A0_conv << 1);
  // To do: Output the "Fref" to Serial interface in Hz
  Serial.print("BINary data A0_ready: ");
  Serial.println(A0_ready, BIN);

  Serial.print("Speed ref in Hz: ");
  Serial.println(SR_SPEED_CTRL_RES_1_6 * A0_ready, DEC);
  // To do: Sent SPI data to "ADDR_WRT_ONLY"
  foo = (ADDR_WRT_ONLY | A0_ready);
  count = countSetBits(foo);

  if ((count % 2) == 0) {
    foo2 = (foo | PARITY);

    SPI.beginTransaction(SPISettings(SPI_SPEED, MSBFIRST, SPI_MODE3));
    digitalWrite(PIN_CS, LOW);
    SPI.transfer16(foo2);
    digitalWrite(PIN_CS, HIGH);
  }
  else {

    SPI.beginTransaction(SPISettings(SPI_SPEED, MSBFIRST, SPI_MODE3));
    digitalWrite(PIN_CS, LOW);
    SPI.transfer16(foo);
    digitalWrite(PIN_CS, HIGH);
  }
}


void setup() {

  SPI.begin();
  pinMode(PIN_CS, OUTPUT);

  Serial.begin(115200);
  delay(100);

  writeregisters();
}

void loop() {

  temperature();
  voltage();
  current();
  showspeed();
  duty_cycle();
  applied_phase_advance();
  speedreference();
  Serial.println();
  delay(200);
}

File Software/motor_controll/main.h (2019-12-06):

/////////SPI CONFIG////////////////////
#define PIN_CS 10
#define SPI_SPEED 20000000
//#define PIN_D9 9 // Used for PWM
unsigned long duty1,duty2;
// Duty Cycle in terms of a percentage.
unsigned long plus;
// Value read from A1, in case plus mode is activated
float xxx;
// Float numbers to calculate duty for PWM 1 and PWM 2
float yyy;
unsigned long pwm1;
// Value read from A0 and A2 to give PWM duty cycle output in terms // of 0-5V
unsigned long pwm2;

/////////REGISTER MODE SELECTION //////
const uint16_t SPI_WRITE (1 << 10);
const uint16_t SPI_READ (0 << 10);
/////////REGISTER MODE SELECTION END////

///////////REGISTER ADDRES//////////////
uint16_t ADDR_PWM_CONF_0 = 0x000;
uint16_t ADDR_PWM_CONF_1 = 0x800;
uint16_t ADDR_BRGE_CONF = 0x1000;
uint16_t ADDR_GATE_DRV_CONF_0 = 0x1800;
uint16_t ADDR_GATE_DRV_CONF_1 = 0x2000;
uint16_t ADDR_GATE_DRV_CONF_2 = 0x2800;
uint16_t ADDR_I_LIM_CONF = 0x3000;
uint16_t ADDR_VDS_0 = 0x3800;
uint16_t ADDR_VDS_1 = 0x4000;
uint16_t ADDR_WATCH_DOG_0 = 0x4800;
uint16_t ADDR_WATCH_DOG_1 = 0x5000;
uint16_t ADDR_COMMT_0 = 0x5800;
uint16_t ADDR_COMMT_1 = 0x6000;
uint16_t ADDR_BEMF_CONF_0 = 0x6800;
uint16_t ADDR_BEMF_CONF_1 = 0x7000;
uint16_t ADDR_STR_CONF_0 = 0x7800;
uint16_t ADDR_STR_CONF_1 = 0x8000;
uint16_t ADDR_STR_CONF_2 = 0x8800;
uint16_t ADDR_STR_CONF_3 = 0x9000;
uint16_t ADDR_STR_CONF_4 = 0x9800;
uint16_t ADDR_STR_CONF_5 = 0xA000;
uint16_t ADDR_SPEED_LOOP_0 = 0xA800;
uint16_t ADDR_SPEED_LOOP_1 = 0xB000;
uint16_t ADDR_SPEED_LOOP_2 = 0xB800;
uint16_t ADDR_NVM_WR = 0xC000;
uint16_t ADDR_SYS = 0xC800;
uint16_t ADDR_PHA_ADV = 0xD000;
uint16_t ADDR_MOT_FUN = 0xD800;
uint16_t ADDR_MASK = 0xE000;
uint16_t ADDR_RDBACK_SEL = 0xE800;
uint16_t ADDR_WRT_ONLY = 0xF000;
uint16_t ADDR_RD_ONLY = 0xF800;
/////////REGISTER ADDRES END///////////
/////////DEF VAL CONF//////////////////
//uint16_t PWM_CONF_0_DEF = 0x4C;
//uint16_t PWM_CONF_0_DEF = 0xFC;
uint16_t PWM_CONF_0_DEF = 0b0011000100;
uint16_t PWM_CONF_1_DEF = 0b0000000000;
uint16_t BRGE_CONF_DEF = 0b0000101000;
//uint16_t GATE_DRV_CONF_0_DEF = 0x82;
//uint16_t GATE_DRV_CONF_1_DEF = 0xC3;
//uint16_t GATE_DRV_CONF_2_DEF = 0x6C;
uint16_t GATE_DRV_CONF_0_DEF = 0b0100000100;
uint16_t GATE_DRV_CONF_1_DEF = 0b0110000110;
uint16_t GATE_DRV_CONF_2_DEF = 0b0011011000;

uint16_t I_LIM_CONF_DEF = 0x10F;
uint16_t VDS_0_DEF = 0x18;
uint16_t VDS_1_DEF = 0x18;
//uint16_t WATCH_DOG_0_DEF = 0xA;
//uint16_t WATCH_DOG_1_DEF = 0x14A;
uint16_t WATCH_DOG_0_DEF = 0b0000000000;
uint16_t WATCH_DOG_1_DEF = 0b0000000000;  //Disables the Watchdog

uint16_t COMMT_0_DEF = 0x88;
uint16_t COMMT_1_DEF = 0x88;
uint16_t BEMF_CONF_0_DEF = 0x0;
uint16_t BEMF_CONF_1_DEF = 0x66; //1100110
//uint16_t STR_CONF_0_DEF = 0x4A;
uint16_t STR_CONF_0_DEF = 0b0000111110;
uint16_t STR_CONF_1_DEF = 0b1000010000; //0000 //REG 16
uint16_t STR_CONF_2_DEF = 0x230;
uint16_t STR_CONF_3_DEF = 0x22;
//uint16_t STR_CONF_4_DEF = 0x22;
uint16_t STR_CONF_4_DEF = 0b0000100010;
uint16_t STR_CONF_5_DEF = 0xE;
uint16_t SPEED_LOOP_0_DEF = 0x4A;
uint16_t SPEED_LOOP_1_DEF = 0x80;
uint16_t SPEED_LOOP_1_SR = 0b0010;
uint16_t SPEED_LOOP_2_DEF = 0x77; // Check it out again
//uint16_t NVM_WR_DEF = 0x000;   // DO NOT USE
uint16_t SYS_DEF = 0b0101001010;  // USING OPM = TRUE
//uint16_t SYS_2 = 0xB8;
uint16_t PHA_ADV_DEF = 0x768;
uint16_t MOT_FUN_DEF = 0x2;

// Setup in functions
uint16_t MASK_DEF = 0x100; // READ ONLY
//uint16_t RDBACK_SEL_DEF = 0x100; // Check it out again
uint16_t WRT_ONLY_DEF = 0b0000000000;
uint16_t RD_ONLY_DEF = 0x000;  // Setup it manualiy
/////////DEF VAL CONF END//////////////
/////////READ BACK SELECT DEFINES//////
uint16_t RBS_SEL_DIAG = 0x000;
uint16_t RBS_SEL_MOTOR_SPEED = 0x2;
uint16_t RBS_SEL_IAVG = 0x4;
uint16_t RBS_SEL_VOLT = 0x6;
uint16_t RBS_SEL_TEMP = 0x8;
uint16_t RBS_SEL_DEM_IN = 0xA;
uint16_t RBS_SEL_DUTY_CYC = 0xC;
uint16_t RBS_SEL_PHASE_ADVC = 0xE;
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

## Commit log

2019-11-22 Software added.
    Chip test programm and motor controll programm added
2020-04-22 minor changes
    Added ploted schematic, fixed errors.
